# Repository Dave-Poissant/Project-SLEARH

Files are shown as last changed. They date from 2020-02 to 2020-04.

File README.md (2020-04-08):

# Project-SLEARH
Articulated robotic hand designed for sign language education

# Preriquisites:
Hardware:
  - Arduino Mega 2560;
  - 1 usb to printer type cable;
  - 1 drive for the motors ( (PCA-96 85) link: https://www.sunfounder.com/pca9685-16-channel-12-bit-pwm-servo-driver.html);
  - 12 electrical step motors ((TowerPro SG90 Mini-engrenage Micro Servo 9g) link: https://lamassue.fr/product/towerpro-sg90-mini-engrenage-micro-servo-9g/);
  - RaspberryPi 3B+;
  - Micro-SD card (for RPi image);
  
Software;
  - Python 3.7(installed for this gitProject, but not necessarily needed);
  - Python Library:
    - pySerial;
    - tkinter;
  - Arduino IDE for the compiler;
  - Arduino Library:
    - Adafruit_PWMServoDriver.h;
    - ArduinoJson.h;
    - Wire.h;
    (But they all should be downloaded with the plateformio.ini)
    
# Steps to start your project:
  - Read the Mechanics/README.md for informations on how to build the hand;
  - Read the Electrics/README.md for informations on how to plug the motors and the drive on the arduino;
  - Install your favorite python IDE;
  - Open this git repo in a new project and create a python RunTool for UI_Main_Script.py script (that's where the application starts);
  - Install pySerial on your computer (it will appears in your python <python path>/Lib/*);
  (Now, your python side of the project should be up to run)
  - Install VsCode on your computer;
  - Install plateformio and ArduinoIDE in your vscode;
  - Set your Arduino_debug.exe path in your VsCode setups;
  - Build the project one first time (and it should load all the needed libraries);
  (Now, your Arduino side of the project should be up to run)

  - Plug the Arduino to your computer and start the UI_Main_Script.py to start the application and the Arduino thread!
  
 # Steps to be able to run to application on the Raspberry Pi 3b+
  - Flash your Micro-SD card with an up to date RPi image running a linux operating system (you can flash your Micro-SD card with this       tool: https://www.balena.io/etcher/);
  - Connect your Micro-SD card in your RPi and open it with an internet cable or via VMWare for example;
  - On the first RPi's run, set your preferences;
  - Now, open a terminal and instal python 3.6 (or niewer, this could take some time) (this link could be usefull: https://github.com/instabot-py/instabot.py/wiki/Installing-Python-3.7-on-Raspberry-Pi);
  - Install the PySerial library with:
    $ sudo apt-get install pyserial
  - If you're connected to your RPi via VMWare or ssh, run this command:
    - $ export DISPLAY=:0
  - Create your project directory where you want it on your RPi:
    - $ cd "DIRECTORY PATH"
    - $ mkdir "PROJECT NAME"
    - $ cd "PROJECT NAME"
    - $ git clone "THE PROJECT'S LINK"
    - $ git pull
  - The project should now be copied locally onto your RPi;
  
  - Now go to the project's Ui_Main_script.py path on your RPi and run the program through a terminal:
    - $ python Ui_Main_Script.py
  
# Now Have Fun !

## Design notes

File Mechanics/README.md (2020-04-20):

ASSEMBLY OF THE HAND

1. Start by opening the BOM file in this folder.
2. With a 3D printer at 40% fill and supports, print all the parts that have &quot;3D printed&quot; as a link. Some parts need to be printed more than once, refer to the quantity column of the BOM to know how many.
3. Make sure you have at your disposition all the fasteners needed for the assembly. The specs and the quantity needed are given in the BOM. If you need to buy anything, there is a McMaster link for each part.
4. Separate all the printed parts for each of the fingers where each number is the index in the BOM;

Pinky: 4 – 1 – 12 – 7

Ring finger: 4 – 1 – 12 – 3

Middle finger: 4 – 1 – 12 – 5

Index finger: 4 – 1 – 12 – 3

Thumb: 8 – 9 – 10 – 11 – 27 - 28

1. For the pinky, attach the two phalanxes together at the joint with the bolt of index 17 and the nut of index 19.
2. Assemble a servomotor to the servosocket with the fasteners 24. Make sure the wires are towards the hand.
3. Install the second lever arm on the servomotor with the bolt of index 15 and the nut of index 16. Make sure the curve of the rod is toward the back of the finger, that the head of the bolt is toward the servomotor and that you use the small hole of the rod.
4. Attach the other end of the rod to the last phalanx with the bolt of index 18 and the nut of index 19.
5. Attach the first lever arm of index 1 on the small arm of the first phalanx with the bolt of index 18 and the nut of index 19. Make sure the rod is towards the outside of the phalanx, that you use the bigger hole of the rod and that the curve is towards the back of the finger.
6. Repeat the steps 5-9 for each of the other fingers except for the thumb.
7. For the thumb, attach the two last phalanxes together at the joint with the bolt of index 17 and the nut of index 19.
8. Assemble a servomotor to the two servosockets of the thumb with the fasteners 24. Make sure the wires are towards the hand.
9. Install the third lever arm on the servomotor of the second servosocket with the bolt of index 15 and the nut of index 16. Make sure the curve of the rod is toward the back of the finger, that the head of the bolt is toward the servomotor and that you use the small hole of the rod.
10. Attach the other end of the rod to the last phalanx with the bolt of index 18 and the nut of index 19.
11. Install the second lever arm on the servomotor of the first servosocket with the bolt of index 15 and the nut of index 16. Make sure the curve of the rod is toward the back of the finger, that the head of the bolt is toward the servomotor and that you use the small hole of the rod.
12. Attach the other end of the rod to the second phalanx with the bolt of index 18 and the nut of index 19.
13. Attach the first lever arm on the small arm of the first phalanx with the bolt of index 25 and the nut of index 26. Make sure the rod is towards the back of the phalanx, that you use the bigger hole of the rod and that the curve is towards the outside of the finger.
14. Install a servomotor in each of the 4 servo holders for the palm (index 6). Use the fasteners 24 and make sure that it is installed so that viewed from the top of the servomotor, the wires go to the right.
15. Install the four assemblies made at step 19 on the palm with the fasteners of index 24. Make sure the arms of the servomotors are towards the thumb and that the wires are towards the base of the hand.
16. Install a servomotor on the palm at its spot near the thumb joint. Make sure the wires go towards the hand.
17. Install all the fingers except of the thumb on the palm, use the bolt of index 17 and the nut of index 19.
18. Install the thumb on the palm with the bolt of index 25 and the nut of index 26.
19. Install the lever arms of the fingers on the servomotors of the palm with the bolt of index 15 and the nut of index 16.
20. Install the motors drive on the back of the hand with the four bolts of index 23.
21. Make all the electric connections as explained in the electric README.
22. With three bolts of index 15, install a «+» shape servomotor arm on the base of the palm.
23. With the bolts of index 20, install the Arduino and the raspberry pi on the base of the arm.
24. Install the arm on the base with four bolts of index 20.
25. Install the last servo at the top of the arm with fasteners of index 24.
26. Pass all the wires of the hand inside the arm and make the connections as explained in the electric README.
27. Install the hand on the servomotor.

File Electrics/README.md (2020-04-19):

# Electrical Parts list

    Name	              Description	                                Quantity
    ------------------------------------------------------------------------
    Arduino board	      Arduino Mega 2560	                              1
    Servo driver	      PCA9685 16 channel PWM servo Driver	          1
    Servo motors	      SG90 servo motor	                              12

# Electrical Connections:

  # Arduino pins:
    - 5V:         Ard1 -------> Dr6
    - Gnd:        Ard2 -------> Dr3
    - Vin:        Ard3 -------> Dr7
    - Gnd:        Ard4 -------> Dr1
    - 5V:         Ard5 -------> Dr2
    - scl(pin21): Ard6 -------> Dr4
    - sda(pin20): Ard7 -------> Dr5
    
  # Drive pins:
    - Gnd:        Dr1 --------> Ard4
    - V+:         Dr2 --------> Ard5
    - Gnd:        Dr3 --------> Ard2
    - scl         Dr4 --------> Ard6
    - sda         Dr5 --------> Ard7
    - Vcc         Dr6 --------> Ard1
    - V+          Dr7 --------> Ard3
    
    - 0           Dr8 --------> motor 0
    - 1           Dr9 --------> motor 1
    - 2           Dr10 -------> motor 2
    - 3           Dr11 -------> motor 3
    - 4           Dr12 -------> motor 4
    - 5           Dr13 -------> motor 5
    - 6           Dr14 -------> motor 6
    - 7           Dr15 -------> motor 7
    - 8           Dr16 -------> motor 8
    - 9           Dr17 -------> motor 9

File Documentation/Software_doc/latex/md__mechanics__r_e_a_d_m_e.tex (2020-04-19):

A\+S\+S\+E\+M\+B\+LY OF T\+HE H\+A\+ND

\begin{DoxyEnumerate}
\item Start by 3D printing all the parts of this folder.
\item Separate the pieces for each of the fingers.
\item Put the Servomotors in each of the 10 sockets with the screws with the cables going to the hand.
\item For each finger, assemble the two phalanxes together with a 1/8\textquotesingle{}\textquotesingle{} bolt and a nut.
\item For the servomotors in the fingers, attach the small hole of the small rod with a 1/16\textquotesingle{}\textquotesingle{} bolt and a nut.
\item Attach the other end of the small rod to the upside attach of the distant phalanx.
\item Attach the finger to the palm with a 1/8\textquotesingle{}\textquotesingle{} bolt and a nut.
\item Attach the big hole of the big rod on the attach of the first phalanx of each finger with a 1/8\textquotesingle{}\textquotesingle{} rod and a nut.
\item Attach the last hole of the big rod on the servomotor with a 1/16\textquotesingle{}\textquotesingle{} bolt and a nut. 
\end{DoxyEnumerate}

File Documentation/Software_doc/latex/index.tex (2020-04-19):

\hypertarget{index_Python}{}\doxysection{Python}\label{index_Python}
The Python code englobe the UI and the back-\/end of if\hypertarget{index_Arduino}{}\doxysection{Arduino}\label{index_Arduino}
The Arduino code englobe the function related to motors control sign execution

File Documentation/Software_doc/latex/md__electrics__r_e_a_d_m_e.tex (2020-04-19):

\hypertarget{md__electrics__r_e_a_d_m_e_autotoc_md1}{}\doxysection{Arduino pins\+:}\label{md__electrics__r_e_a_d_m_e_autotoc_md1}

\begin{DoxyItemize}
\item 5V\+: Ard1 -\/-\/-\/-\/---$>$ Dr6
\item Gnd\+: Ard2 -\/-\/-\/-\/---$>$ Dr3
\item Vin\+: Ard3 -\/-\/-\/-\/---$>$ Dr7
\item Gnd\+: Ard4 -\/-\/-\/-\/---$>$ Dr1
\item 5V\+: Ard5 -\/-\/-\/-\/---$>$ Dr2
\item scl(pin21)\+: Ard6 -\/-\/-\/-\/---$>$ Dr4
\item sda(pin20)\+: Ard7 -\/-\/-\/-\/---$>$ Dr5
\end{DoxyItemize}\hypertarget{md__electrics__r_e_a_d_m_e_autotoc_md2}{}\doxysection{Drive pins\+:}\label{md__electrics__r_e_a_d_m_e_autotoc_md2}

\begin{DoxyItemize}
\item Gnd\+: Dr1 -\/-\/-\/-\/-\/---$>$ Ard4
\item V+\+: Dr2 -\/-\/-\/-\/-\/---$>$ Ard5
\item Gnd\+: Dr3 -\/-\/-\/-\/-\/---$>$ Ard2
\item scl Dr4 -\/-\/-\/-\/-\/---$>$ Ard6
\item sda Dr5 -\/-\/-\/-\/-\/---$>$ Ard7
\item Vcc Dr6 -\/-\/-\/-\/-\/---$>$ Ard1
\item V+ Dr7 -\/-\/-\/-\/-\/---$>$ Ard3
\item 0 Dr8 -\/-\/-\/-\/-\/---$>$ motor 0
\item 1 Dr9 -\/-\/-\/-\/-\/---$>$ motor 1
\item 2 Dr10 -\/-\/-\/-\/---$>$ motor 2
\item 3 Dr11 -\/-\/-\/-\/---$>$ motor 3
\item 4 Dr12 -\/-\/-\/-\/---$>$ motor 4
\item 5 Dr13 -\/-\/-\/-\/---$>$ motor 5
\item 6 Dr14 -\/-\/-\/-\/---$>$ motor 6
\item 7 Dr15 -\/-\/-\/-\/---$>$ motor 7
\item 8 Dr16 -\/-\/-\/-\/---$>$ motor 8
\item 9 Dr17 -\/-\/-\/-\/---$>$ motor 9 
\end{DoxyItemize}

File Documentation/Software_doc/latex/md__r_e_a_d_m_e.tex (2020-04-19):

Articulated robotic hand designed for sign language education\hypertarget{md__r_e_a_d_m_e_autotoc_md4}{}\doxysection{Preriquisites\+:}\label{md__r_e_a_d_m_e_autotoc_md4}
Hardware\+:
\begin{DoxyItemize}
\item Arduino Mega 2560;
\item 1 usb to printer type cable;
\item 1 drive for the motors ( (P\+C\+A-\/96 85) link\+: \href{https://www.sunfounder.com/pca9685-16-channel-12-bit-pwm-servo-driver.html}{\texttt{ https\+://www.\+sunfounder.\+com/pca9685-\/16-\/channel-\/12-\/bit-\/pwm-\/servo-\/driver.\+html}});
\item 12 electrical step motors ((Tower\+Pro S\+G90 Mini-\/engrenage Micro \mbox{\hyperlink{class_servo}{Servo}} 9g) link\+: \href{https://lamassue.fr/product/towerpro-sg90-mini-engrenage-micro-servo-9g/}{\texttt{ https\+://lamassue.\+fr/product/towerpro-\/sg90-\/mini-\/engrenage-\/micro-\/servo-\/9g/}});
\item Raspberry\+Pi 3B+;
\item Micro-\/\+SD card (for R\+Pi image);
\end{DoxyItemize}

Software;
\begin{DoxyItemize}
\item Python 3.\+7(installed for this git\+Project, but not necessarily needed);
\item Python Library\+:
\begin{DoxyItemize}
\item py\+Serial;
\item tkinter;
\end{DoxyItemize}
\item Arduino I\+DE for the compiler;
\item Arduino Library\+:
\begin{DoxyItemize}
\item Adafruit\+\_\+\+P\+W\+M\+Servo\+Driver.\+h;
\item Arduino\+Json.\+h;
\item Wire.\+h; (But they all should be downloaded with the plateformio.\+ini)
\end{DoxyItemize}
\end{DoxyItemize}\hypertarget{md__r_e_a_d_m_e_autotoc_md5}{}\doxysection{Steps to start your project\+:}\label{md__r_e_a_d_m_e_autotoc_md5}

\begin{DoxyItemize}
\item Read the Mechanics/\+R\+E\+A\+D\+M\+E.\+md for informations on how to build the hand;
\item Read the Electrics/\+R\+E\+A\+D\+M\+E.\+md for informations on how to plug the motors and the drive on the arduino;
\item Install your favorite python I\+DE;
\item Open this git repo in a new project and create a python Run\+Tool for U\+I\+\_\+\+Main\+\_\+\+Script.\+py script (that\textquotesingle{}s where the application starts);
\item Install py\+Serial on your computer (it will appears in your python $<$python path$>$/\+Lib/$\ast$); (Now, your python side of the project should be up to run)
\item Install Vs\+Code on your computer;
\item Install plateformio and Arduino\+I\+DE in your vscode;
\item Set your Arduino\+\_\+debug.\+exe path in your Vs\+Code setups;
\item Build the project one first time (and it should load all the needed libraries); (Now, your Arduino side of the project should be up to run)
\item Plug the Arduino to your computer and start the U\+I\+\_\+\+Main\+\_\+\+Script.\+py to start the application and the Arduino thread!
\end{DoxyItemize}\hypertarget{md__r_e_a_d_m_e_autotoc_md6}{}\doxysection{Steps to be able to run to application on the Raspberry Pi 3b+}\label{md__r_e_a_d_m_e_autotoc_md6}

\begin{DoxyItemize}
\item Flash your Micro-\/\+SD card with an up to date R\+Pi image running a linux operating system (you can flash your Micro-\/\+SD card with this tool\+: \href{https://www.balena.io/etcher/}{\texttt{ https\+://www.\+balena.\+io/etcher/}});
\item Connect your Micro-\/\+SD card in your R\+Pi and open it with an internet cable or via V\+M\+Ware for example;
\item On the first R\+Pi\textquotesingle{}s run, set your preferences;
\item Now, open a terminal and instal python 3.\+6 (or niewer, this could take some time) (this link could be usefull\+: \href{https://github.com/instabot-py/instabot.py/wiki/Installing-Python-3.7-on-Raspberry-Pi}{\texttt{ https\+://github.\+com/instabot-\/py/instabot.\+py/wiki/\+Installing-\/\+Python-\/3.\+7-\/on-\/\+Raspberry-\/\+Pi}});
\item Install the Py\+Serial library with\+: \$ sudo apt-\/get install pyserial
\item If you\textquotesingle{}re connected to your R\+Pi via V\+M\+Ware or ssh, run this command\+:
\begin{DoxyItemize}
\item \$ export D\+I\+S\+P\+L\+AY=\+:0
\end{DoxyItemize}
\item Create your project directory where you want it on your R\+Pi\+:
\begin{DoxyItemize}
\item \$ cd \char`\"{}\+D\+I\+R\+E\+C\+T\+O\+R\+Y P\+A\+T\+H\char`\"{}
\item \$ mkdir \char`\"{}\+P\+R\+O\+J\+E\+C\+T N\+A\+M\+E\char`\"{}
\item \$ cd \char`\"{}\+P\+R\+O\+J\+E\+C\+T N\+A\+M\+E\char`\"{}
\item \$ git clone \char`\"{}\+T\+H\+E P\+R\+O\+J\+E\+C\+T\textquotesingle{}\+S L\+I\+N\+K\char`\"{}
\item \$ git pull
\end{DoxyItemize}
\item The project should now be copied locally onto your R\+Pi;
\item Now go to the project\textquotesingle{}s Ui\+\_\+\+Main\+\_\+script.\+py path on your R\+Pi and run the program through a terminal\+:
\begin{DoxyItemize}
\item \$ python Ui\+\_\+\+Main\+\_\+\+Script.\+py
\end{DoxyItemize}
\end{DoxyItemize}\hypertarget{md__r_e_a_d_m_e_autotoc_md7}{}\doxysection{Now Have Fun !}\label{md__r_e_a_d_m_e_autotoc_md7}

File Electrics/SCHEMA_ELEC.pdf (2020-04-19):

SDA
SCL

5V

GND

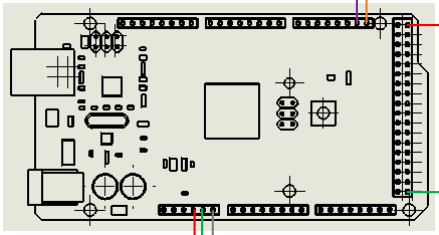
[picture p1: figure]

Vin
5V
GND

ARDUINO MEGA 2560

SERVO SG90

1
SERVO SG90

2
SERVO SG90

3
SERVO SG90

4
SERVO SG90

5
SERVO SG90

6
SERVO SG90

7
SERVO SG90

8
SERVO SG90

9
SERVO SG90

-10
SERVO SG90

-11
SERVO SG90

-12

PCA9685
16 CHANNEL 12

-BIT PWM
I2C ADDRESS l[A5..A0][R/W] VDD : 2.3

-5.5V IO : 5V SAFE
OUTPUT : 25mA EACH/400mA TOTAL GND
SDA
SCL
#OE

VCC
V+

EXTCLK
A0
A1
A2
A3
A4
A5

GND

PWM0
PWM1
PWM2
PWM3
PWM4
PWM5
PWM6
PWM7
PWM8
PWM9
PWM10
PWM11
PWM12
PWM13
PWM14
PWM15
AUXILIARY POWER
V+
GND
GND EXTCLK WHEN NOT IN USE

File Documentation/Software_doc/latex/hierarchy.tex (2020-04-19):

\doxysection{Class Hierarchy}
This inheritance list is sorted roughly, but not completely, alphabetically\+:\begin{DoxyCompactList}
\item \contentsline{section}{character}{\pageref{structcharacter}}{}
\item \contentsline{section}{Python\+\_\+project.\+Backend\+\_\+\+Scripts.\+Communication.\+Communication}{\pageref{class_python__project_1_1_backend___scripts_1_1_communication_1_1_communication}}{}
\item \contentsline{section}{Communication\+Arduino}{\pageref{class_communication_arduino}}{}
\item \contentsline{section}{Python\+\_\+project.\+Backend\+\_\+\+Scripts.\+Configuration.\+Configuration}{\pageref{class_python__project_1_1_backend___scripts_1_1_configuration_1_1_configuration}}{}
\item \contentsline{section}{Python\+\_\+project.\+Backend\+\_\+\+Scripts.\+Event.\+Event}{\pageref{class_python__project_1_1_backend___scripts_1_1_event_1_1_event}}{}
\item \contentsline{section}{Python\+\_\+project.\+Backend\+\_\+\+Scripts.\+Event\+Handler.\+Event\+Handler}{\pageref{class_python__project_1_1_backend___scripts_1_1_event_handler_1_1_event_handler}}{}
\item \contentsline{section}{Python\+\_\+project.\+Backend\+\_\+\+Scripts.\+Event\+Queue.\+Event\+Queue}{\pageref{class_python__project_1_1_backend___scripts_1_1_event_queue_1_1_event_queue}}{}
\item Frame\begin{DoxyCompactList}
\item \contentsline{section}{Python\+\_\+project.\+Ui\+\_\+\+Main\+\_\+\+Script.\+application}{\pageref{class_python__project_1_1_ui___main___script_1_1application}}{}
\end{DoxyCompactList}
\item \contentsline{section}{Python\+\_\+project.\+Backend\+\_\+\+Scripts.\+Quiz.\+Quiz}{\pageref{class_python__project_1_1_backend___scripts_1_1_quiz_1_1_quiz}}{}
\item \contentsline{section}{Servo}{\pageref{class_servo}}{}
\item \contentsline{section}{Soft\+Timer}{\pageref{class_soft_timer}}{}
\item \contentsline{section}{Python\+\_\+project.\+Backend\+\_\+\+Scripts.\+Text\+Analyser.\+Text\+Analyser}{\pageref{class_python__project_1_1_backend___scripts_1_1_text_analyser_1_1_text_analyser}}{}
\item Enum\begin{DoxyCompactList}
\item \contentsline{section}{Python\+\_\+project.\+Backend\+\_\+\+Scripts.\+Event\+Type.\+Event\+Type}{\pageref{class_python__project_1_1_backend___scripts_1_1_event_type_1_1_event_type}}{}
\item \contentsline{section}{Python\+\_\+project.\+Backend\+\_\+\+Scripts.\+Logger.\+Color}{\pageref{class_python__project_1_1_backend___scripts_1_1_logger_1_1_color}}{}
\item \contentsline{section}{Python\+\_\+project.\+Backend\+\_\+\+Scripts.\+Purpose.\+Purpose}{\pageref{class_python__project_1_1_backend___scripts_1_1_purpose_1_1_purpose}}{}
\item \contentsline{section}{Python\+\_\+project.\+Ui\+\_\+\+Main\+\_\+\+Script.\+Mode\+Enum}{\pageref{class_python__project_1_1_ui___main___script_1_1_mode_enum}}{}
\item \contentsline{section}{Python\+\_\+project.\+Ui\+\_\+\+Main\+\_\+\+Script.\+Purpose\+Enum}{\pageref{class_python__project_1_1_ui___main___script_1_1_purpose_enum}}{}
\end{DoxyCompactList}
\end{DoxyCompactList}

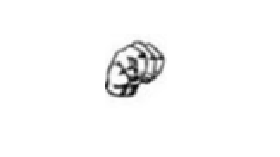
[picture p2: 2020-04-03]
Python_project/Image_Library/Quiz_purpose_img/sign_m.png

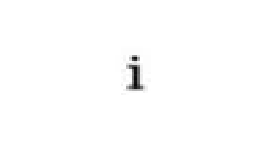
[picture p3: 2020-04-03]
Python_project/Image_Library/Education_purpose_img/letter_i.png

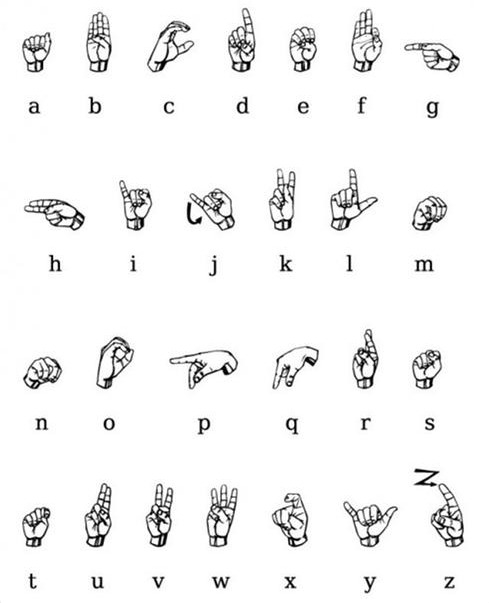
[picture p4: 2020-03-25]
Python_project/Image_Library/all_signs_img.png

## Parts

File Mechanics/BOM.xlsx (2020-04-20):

BOM
index | name | link | qty. | description | directory
1 | joint doigt palm servosocket | 3D printed | 4 | First lever arms for fingers | Project-SLEARH/Mechanics/CAD/CAD Palm/Joint_doigt_Palm-ServoSocket.SLDPRT (https://github.com/Dave-Poissant/Project-SLEARH)
2 | palm v3 | 3D printed | 1 | palm | Project-SLEARH/Mechanics/CAD/CAD Palm/PalmV3.SLDPRT
3 | phalange 2 index-anulaire | 3D printed | 2 | Last part for index and ring finger | Project-SLEARH/Mechanics/CAD/CAD Palm/CAD Index-Annulaire/phalange2_Index-Annulaire.SLDPRT
4 | SG90 Servo socket | 3D printed | 4 | Socket for servo for each finger | Project-SLEARH/Mechanics/CAD/CAD Palm/CAD Majeur/SG90 - Servo Socket.SLDPRT
5 | phalange 2 majeur | 3D printed | 1 | Last part for the middle finger | Project-SLEARH/Mechanics/CAD/CAD Palm/CAD Majeur/phalange2_Majeur.SLDPRT
6 | servoholder | 3D printed | 4 | Servo holders on the palm | Project-SLEARH/Mechanics/CAD/CAD Palm/ServoHolder.SLDPRT
7 | phalange 2 auriculaire | 3D printed | 1 | Last part for the pinky finger | Project-SLEARH/Mechanics/CAD/CAD Palm/CAD Auriculaire/phalange2_Auriculaire.SLDPRT
8 | phalange 2 pouce | 3D printed | 1 | Last part for the thumb | Project-SLEARH/Mechanics/CAD/CAD Palm/CAD Pouce/Pouce/phalange2_Pouce.SLDPRT
9 | Bras de levier pouce | 3D printed | 1 | Last lever arm for the thumb | Project-SLEARH/Mechanics/CAD/CAD Palm/CAD Pouce/Pouce/Bras de levier_Pouce.SLDPRT
10 | Bras de levier pouce 2 | 3D printed | 1 | Second lever arm for the thumb | Project-SLEARH/Mechanics/CAD/CAD Palm/CAD Pouce/Bras de levier_Pouce2.SLDPRT
11 | Bras de levier pouce 3 | 3D printed | 1 | First lever arm for the thumb | Project-SLEARH/Mechanics/CAD/CAD Palm/CAD Pouce/Bras de levier_Pouce3.SLDPRT
12 | Bras de levier | 3D printed | 4 | Second lever arms for fingers | Project-SLEARH/Mechanics/CAD/CAD Palm/CAD Majeur/Bras de levier.SLDPRT
13 | Bras | 3D printed | 1 | Arm | Project-SLEARH/Mechanics/CAD/CAD Socle/Bras.SLDPRT
14 | Base | 3D printed | 1 | Base for the arm | Project-SLEARH/Mechanics/CAD/CAD Socle/Base.SLDPRT
15 | 92453A856 | https://www.mcmaster.com/92453a856 | 15 | 00-90 Thread, 3/8" Long -- lever arm to servo | Project-SLEARH/Mechanics/CAD/CAD Palm/92453A856_BRASS ROUND HEAD SLOTTED MACHINE SCREW.SLDPRT
16 | 90001A403 | https://www.mcmaster.com/90001a403 | 11 | 00-90 Thread Size -- lever arm to servo | Project-SLEARH/Mechanics/CAD/CAD Palm/90001A403_TYPE 18-8 STAINLESS STEEL HEX NUT.SLDPRT
17 | 92196A131 | https://www.mcmaster.com/92196a131 | 10 | 5-40 Thread Size, 3/4" Long -- point pivot of sockets to palm | Project-SLEARH/Mechanics/CAD/CAD Palm/92196A131_18-8 STAINLESS STEEL SOCKET HEAD CAP SCREW.SLDPRT
18 | 91251A130 | https://www.mcmaster.com/91251a130 | 10 | 5-40 Thread Size, 5/8" Long -- lever arms to sockets and tips of fingers | Project-SLEARH/Mechanics/CAD/CAD Palm/91251A130_BLACK-OXIDE ALLOY STEEL SOCKET HEAD CAP SCREW.SLDPRT
19 | 90480A006 | https://www.mcmaster.com/90480a006 | 20 | Zinc-Plated, 5-40 Thread Size -- knot for 14 and 15 | Project-SLEARH/Mechanics/CAD/CAD Palm/90480A006_LOW-STRENGTH STEEL HEX NUT.SLDPRT
20 | 92000A106 | https://www.mcmaster.com/92000a106 | 14 | M2.5 x 0.45mm Thread, 10mm Long -- Arduino Mega, Raspberry Pi and arm | Project-SLEARH/Mechanics/CAD/CAD Socle/92000A106_18-8 SS METRIC PAN HEAD PHIL MACHINE SCREW.SLDPRT
21 | 90480A003 | https://www.mcmaster.com/90480a003 | 1 | Zinc-Plated, 2-56 Thread Size -- first lever arm to socket of the thumb | Project-SLEARH/Mechanics/CAD/CAD Palm/90480A003_LOW-STRENGTH STEEL HEX NUT.SLDPRT
22 | 91251A079 | https://www.mcmaster.com/91251a079 | 1 | 2-56 Thread Size, 3/8" Long -- first lever arm to socket of the thumb | Project-SLEARH/Mechanics/CAD/CAD Palm/91251A079_BLACK-OXIDE ALLOY STEEL SOCKET HEAD CAP SCREW.SLDPRT
23 | 90087A103 | https://www.mcmaster.com/90087a103 | 4 | Zinc-Plated Steel, 2-56 Thread, 3/8" Long -- for drive | Project-SLEARH/Mechanics/CAD/CAD Palm/90087A103_THRD-CUTTING SCREW FOR METAL PLASTIC TYPE F.SLDPRT
24 | 99461A825 | https://www.mcmaster.com/99461a825 | 30 | for Plastic, 18-8 Stainless Steel, Number 3 Size, 3/8" Long -- for servo and servo holders | Project-SLEARH/Mechanics/CAD/CAD Palm/99461A825_THREAD-FORMING SCREW FOR PLASTIC.SLDPRT
25 | 90044A242 | https://www.mcmaster.com/90044a242 | 1 | 2-64 Thread Size, 1" Long -- first joint of thumb | Project-SLEARH/Mechanics/CAD/CAD Palm/90044A242_BLACK-OXIDE ALLOY STEEL SOCKET HEAD SCREW.SLDPRT
26 | 90480A135 | https://www.mcmaster.com/90480a135 | 1 | Zinc-Plated, 2-64 Thread Size -- first joint of thumb | Project-SLEARH/Mechanics/CAD/CAD Palm/90480A135_LOW-STRENGTH STEEL HEX NUT.SLDPRT
27 | SG90 Servo socket pouce | 3D printed | 1 | Second socket for servo for the thumb | Project-SLEARH/Mechanics/CAD/CAD Palm/CAD Pouce/Pouce/SG90 - Servo Socket_Pouce.SLDPRT
28 | SG90 Servo socket pouce 2 | 3D printed | 1 | First socket for servo for the thumb | Project-SLEARH/Mechanics/CAD/CAD Palm/CAD Pouce/SG90 - Servo Socket_Pouce2.SLDPRT

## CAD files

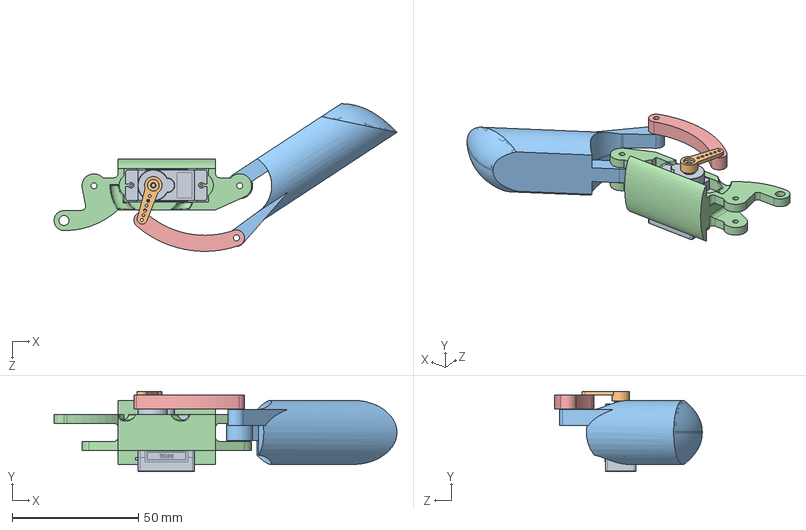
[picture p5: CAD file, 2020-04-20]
Mechanics/CAD/CAD Palm/CAD Index-Annulaire/Index-Annulaire.SLDASM
135.7 x 31.8 x 58.4 mm
SG90 - Micro Servo 9g - Tower Pro.1
SG90 - Micro Servo 9g - Tower Pro.2
phalange2_Index-Annulaire
SG90 - Servo Socket
Bras de levier

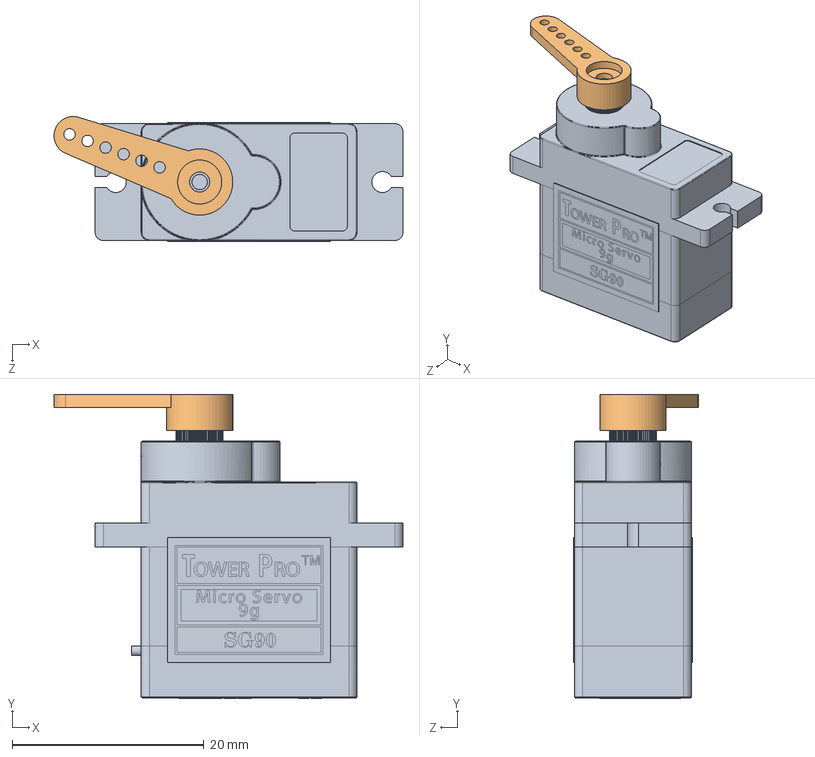
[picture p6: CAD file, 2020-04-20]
Mechanics/CAD/CAD Palm/CAD Majeur/Servo - SG90/SG90 - Micro Servo Assembly.SLDASM
36.4 x 31.8 x 13.0 mm
SG90 - Micro Servo 9g - Tower Pro.1
SG90 - Micro Servo 9g - Tower Pro.2

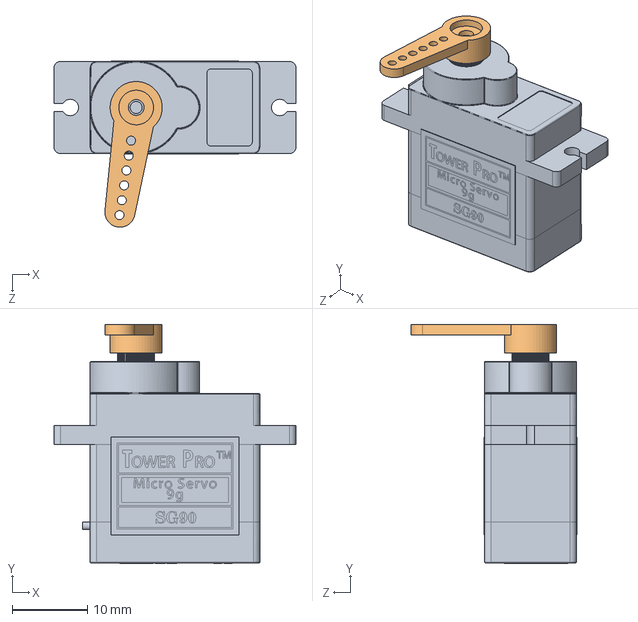
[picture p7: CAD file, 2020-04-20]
Mechanics/CAD/Servo - SG90/SG90 - Micro Servo Assembly.SLDASM
32.1 x 31.8 x 22.1 mm
SG90 - Micro Servo 9g - Tower Pro.1
SG90 - Micro Servo 9g - Tower Pro.2

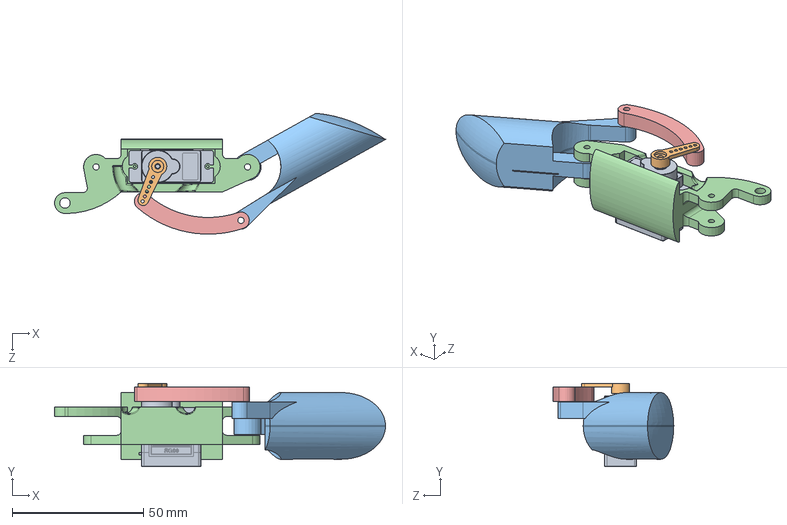
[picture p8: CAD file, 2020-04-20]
Mechanics/CAD/CAD Palm/CAD Auriculaire/Auriculaire.SLDASM
126.0 x 31.7 x 46.1 mm
SG90 - Micro Servo 9g - Tower Pro.1
SG90 - Micro Servo 9g - Tower Pro.2
phalange2_Auriculaire
SG90 - Servo Socket
Bras de levier

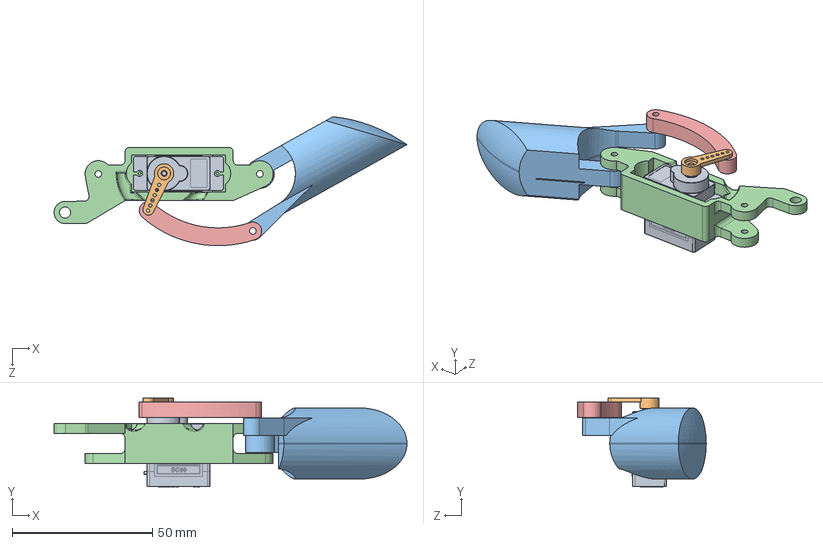
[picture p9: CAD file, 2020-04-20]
Mechanics/CAD/CAD Palm/CAD Majeur/ProximalPhalangeAssem.SLDASM
126.0 x 31.7 x 46.1 mm
SG90 - Micro Servo 9g - Tower Pro.1
SG90 - Micro Servo 9g - Tower Pro.2
phalange2
SG90 - Servo Socket
Bras de levier

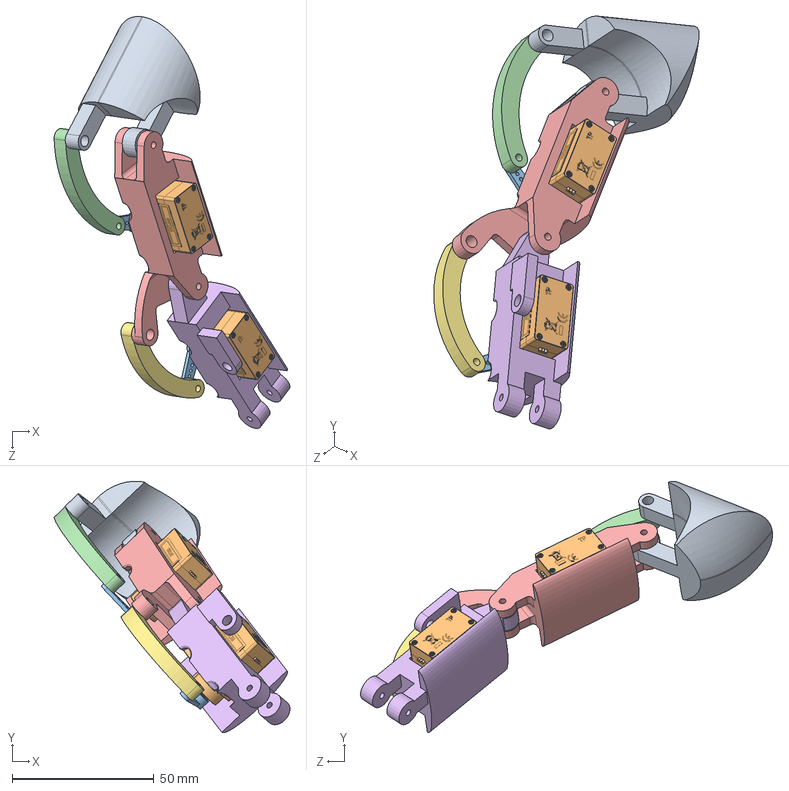
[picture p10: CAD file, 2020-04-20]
Mechanics/CAD/CAD Palm/CAD Pouce/Palm_Thumb_Ass.SLDASM
83.1 x 88.6 x 145.2 mm
phalange2_Pouce
SG90 - Micro Servo 9g - Tower Pro.1 x 2
SG90 - Micro Servo 9g - Tower Pro.2 x 2
Bras de levier_Pouce
SG90 - Servo Socket_Pouce
SG90 - Servo Socket_Pouce2
Bras de levier_Pouce2

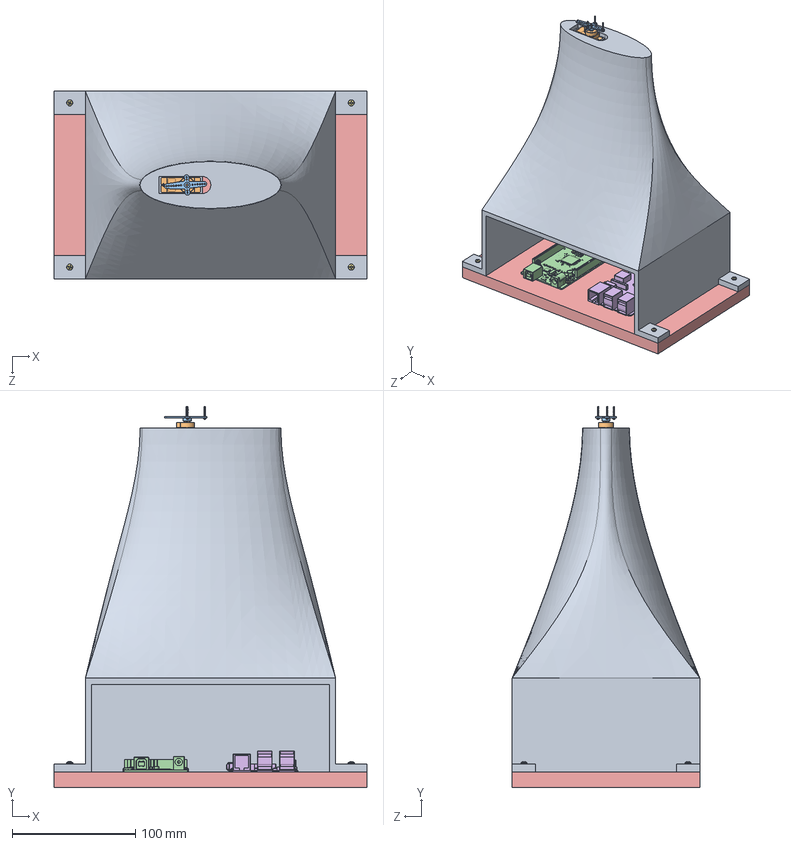
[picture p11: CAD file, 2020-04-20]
Mechanics/CAD/CAD Socle/Arm_Assembly.SLDASM
254.0 x 309.4 x 152.4 mm
Bras
SG90 - Micro Servo 9g - Tower Pro.1
SG90 - Micro Servo 9g - Tower Pro.4
arduinoMega
Base
Raspberrypimodel
92000A106_18-8 SS METRIC PAN HEAD PHIL MACHINE SCREW x 14
92453A856_BRASS ROUND HEAD SLOTTED MACHINE SCREW x 3

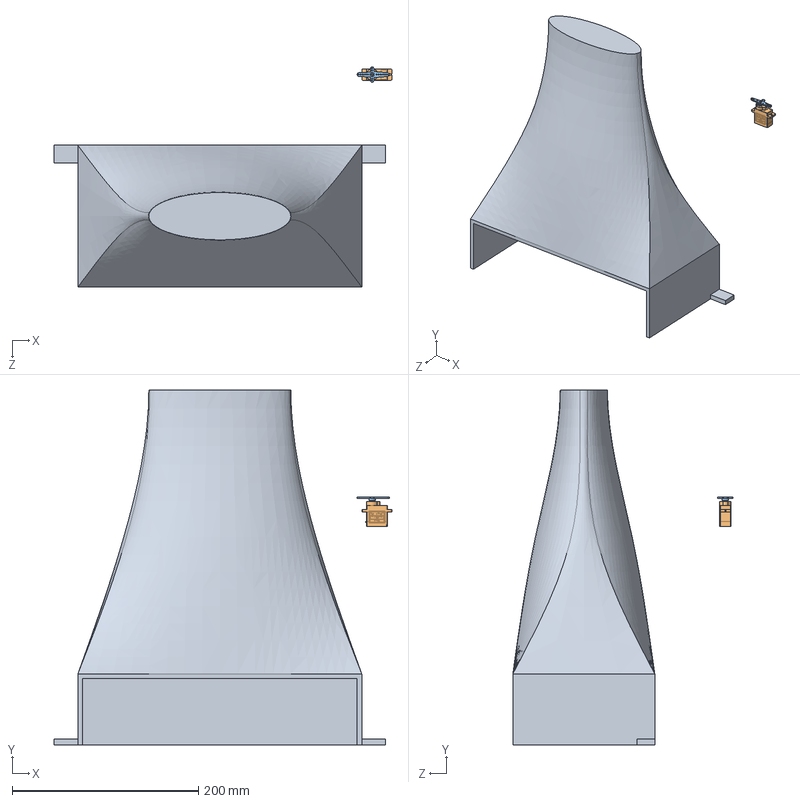
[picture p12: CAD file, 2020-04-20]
Mechanics/CAD/CAD Socle/Servo - SG90/arm_Assembly.SLDASM
362.4 x 381.0 x 236.5 mm
Bras
SG90 - Micro Servo 9g - Tower Pro.1
SG90 - Micro Servo 9g - Tower Pro.4

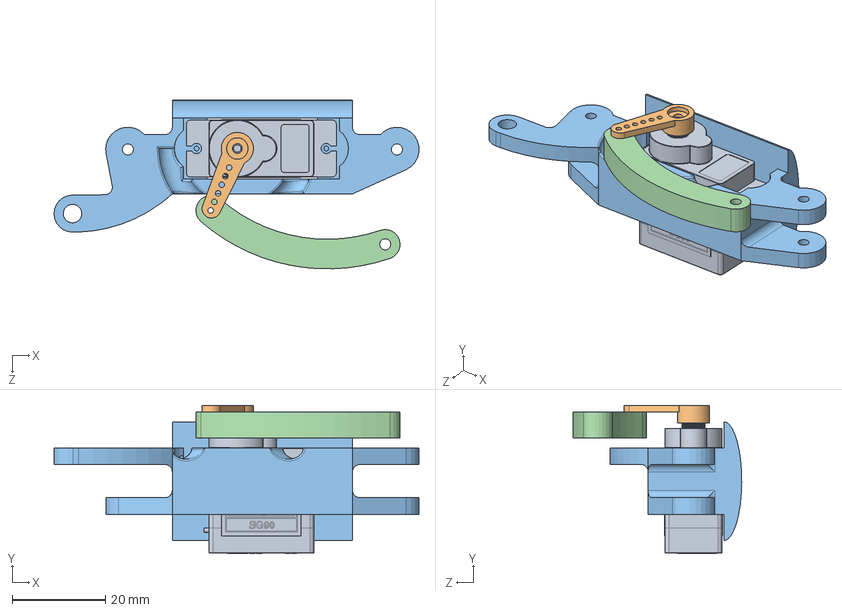
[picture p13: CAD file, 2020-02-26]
Mechanics/CAD/CAD Palm/CAD Majeur/Majeur.SLDASM
78.2 x 31.7 x 36.1 mm
SG90 - Micro Servo 9g - Tower Pro.1
SG90 - Micro Servo 9g - Tower Pro.2
SG90 - Servo Socket
Bras de levier

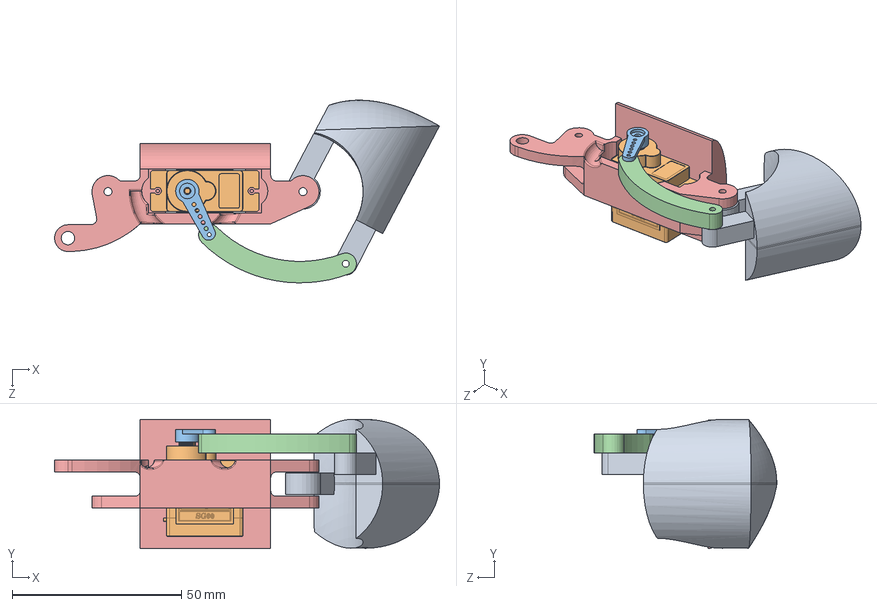
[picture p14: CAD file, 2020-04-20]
Mechanics/CAD/CAD Palm/CAD Pouce/Pouce/Pouce_Ass.SLDASM
113.9 x 38.2 x 54.0 mm
phalange2_Pouce
SG90 - Micro Servo 9g - Tower Pro.1
SG90 - Micro Servo 9g - Tower Pro.2
Bras de levier_Pouce
SG90 - Servo Socket_Pouce

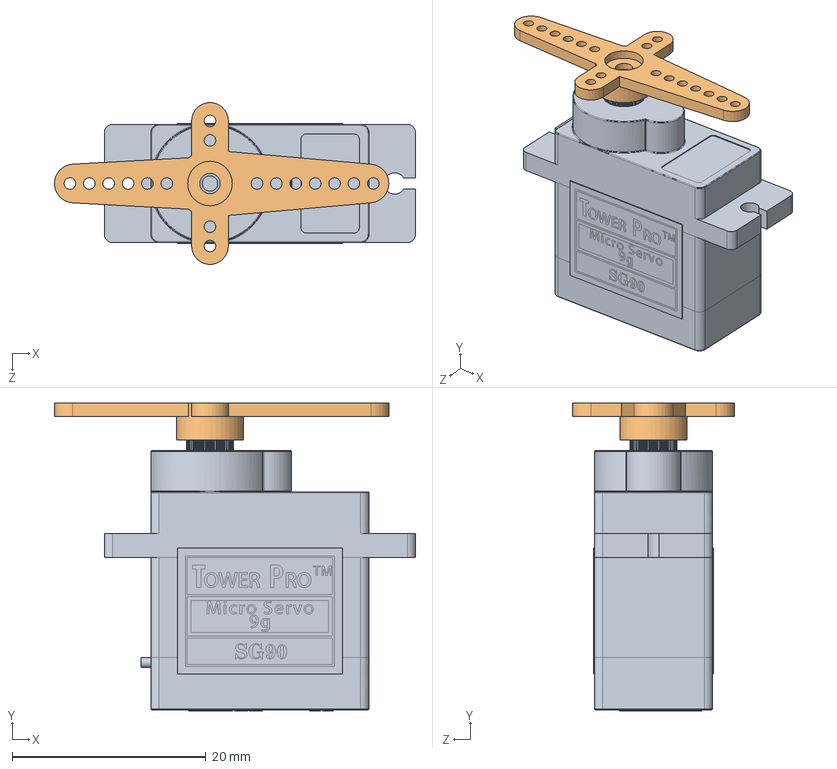
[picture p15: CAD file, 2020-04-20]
Mechanics/CAD/CAD Socle/Servo - SG90/SG90 - Micro Servo Assembly Socle.SLDASM
37.2 x 31.8 x 16.7 mm
SG90 - Micro Servo 9g - Tower Pro.1
SG90 - Micro Servo 9g - Tower Pro.4

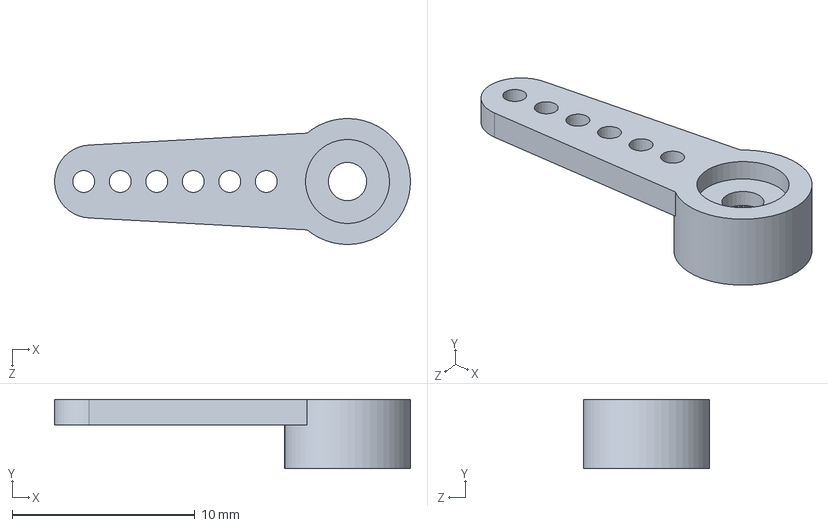
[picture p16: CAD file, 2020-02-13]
Mechanics/CAD/CAD Palm/CAD Auriculaire/Servo - SG90/SG90 - Micro Servo 9g - Tower Pro.2.SLDPRT
19.5 x 3.80 x 6.90 mm

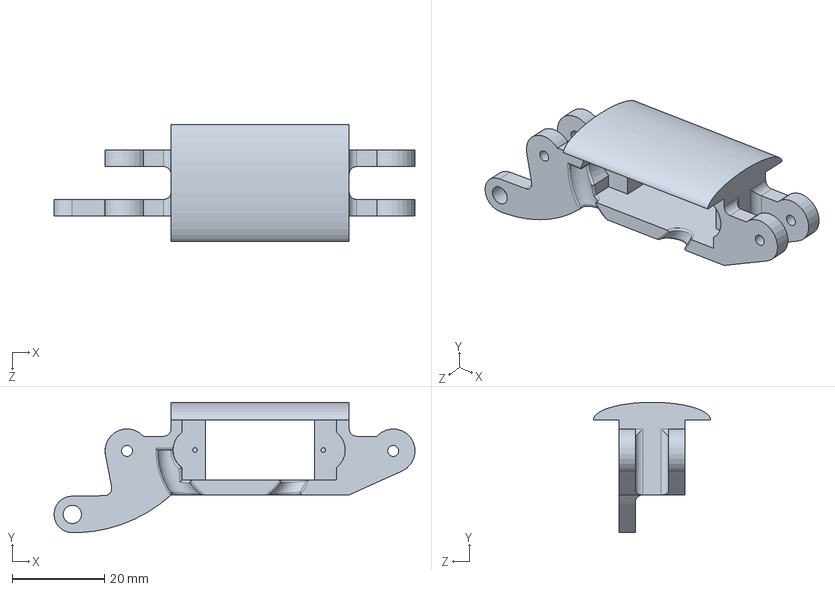
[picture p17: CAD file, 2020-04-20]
Mechanics/CAD/CAD Palm/CAD Auriculaire/SG90 - Servo Socket.SLDPRT
78.2 x 28.3 x 25.4 mm

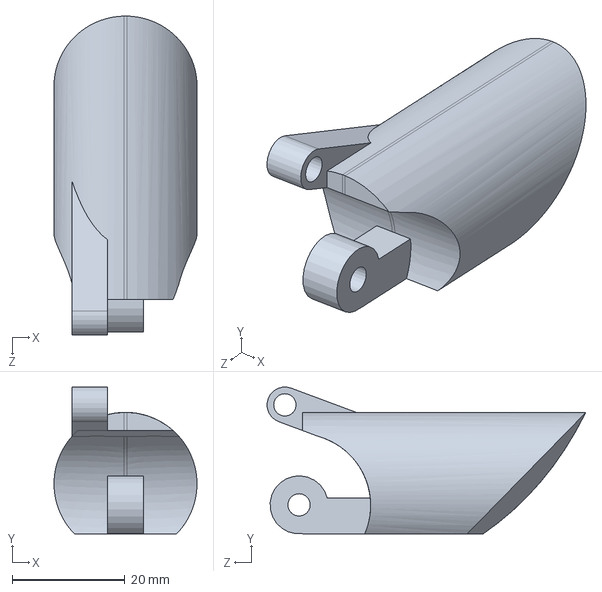
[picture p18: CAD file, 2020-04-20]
Mechanics/CAD/CAD Palm/CAD Majeur/phalange2.SLDPRT
25.4 x 26.1 x 56.6 mm

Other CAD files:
Mechanics/CAD/CAD Palm/CAD Pouce/Servo - SG90/SG90 - Micro Servo Assembly.SLDASM
Mechanics/CAD/CAD Palm/CAD Auriculaire/Servo - SG90/SG90 - Micro Servo Assembly.SLDASM
Mechanics/CAD/CAD Palm/CAD Index-Annulaire/Servo - SG90/SG90 - Micro Servo Assembly.SLDASM
Mechanics/CAD/CAD Palm/90001A403_TYPE 18-8 STAINLESS STEEL HEX NUT.SLDPRT
Mechanics/CAD/CAD Palm/90044A242_BLACK-OXIDE ALLOY STEEL SOCKET HEAD SCREW.SLDPRT
Mechanics/CAD/CAD Palm/90087A103_THRD-CUTTING SCREW FOR METAL PLASTIC TYPE F.SLDPRT
Mechanics/CAD/CAD Palm/90480A003_LOW-STRENGTH STEEL HEX NUT.SLDPRT
Mechanics/CAD/CAD Palm/90480A006_LOW-STRENGTH STEEL HEX NUT.SLDPRT
Mechanics/CAD/CAD Palm/90480A135_LOW-STRENGTH STEEL HEX NUT.SLDPRT
Mechanics/CAD/CAD Palm/91251A079_BLACK-OXIDE ALLOY STEEL SOCKET HEAD CAP SCREW.SLDPRT
Mechanics/CAD/CAD Palm/91251A130_BLACK-OXIDE ALLOY STEEL SOCKET HEAD CAP SCREW.SLDPRT
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

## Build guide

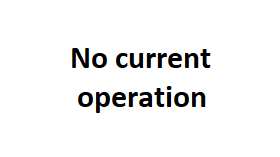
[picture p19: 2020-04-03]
Python_project/Image_Library/no_operation_img.png

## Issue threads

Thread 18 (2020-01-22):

Define user interface needs

bigemfat, 2020-01-22:

Dave-Poissant, 2020-01-22:
-> Indicator that shows the Pi-arduino connection's state;
-> Input text field, for the user;
-> A visual help for the user, to show where the process is;
-> Button to send the text to the back-end;
-> Stop button;
-> Indicator that shows if the hand is currently executing a command or if it's in idle state;
-> Manual mode and "Next letter" button;
-> A glider to select the time it takes before the next letter command is executed (If not in manual mode);
-> (Facultative) Hand simulation to show that the right commands are sent if the physical hand does not work;
-> Pause button;
-> Mode selector (Test/Quiz);
-> Warning of some sort if a letter isn't supported.

Closed 2020-01-29.

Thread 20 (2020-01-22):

Define the Back-End needs

bigemfat, 2020-01-22:

bigemfat, 2020-01-22:
**Needs for Pi :**
1. Parse and validate text input;
2. Connect to Arduino/OpenCR;
3. Update process and connection states (at all times);
4. Send messages to Arduino/OpenCR;
5. Synchronize processes;
6. Handle errors;
7. Handle options/parameters;
8. Emergency stop sequence;
9. Reset sequence;
10. Smoke test sequence (ex: move every motors);

**Need for Arduino/OpenCR :**
1.

Closed 2020-01-29.

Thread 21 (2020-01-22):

Define the back end programming classes and functions

bigemfat, 2020-01-22:

JerSamson, 2020-01-22:
**RaspberryPi classes**

1.  Parser
- Extract characters from the input text box
- Creates Event object
- Sends Events into the "Event table"

2. Event
- Has a name (character)

3. Event Handler
- Has its own thread: Executes the events in its table
- Has a private Event table
- Calls "Send comm."

4. Communication
- Communicates with the Arduino using a mutex lock condition
- Json
- Json string includes Ticket

5. Configuration
- Enum : Parameters / Options
- Has attributes for every parameter

Closed 2020-02-04.

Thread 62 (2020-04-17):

Implement reverse move functionnality and pause between letters on arduino project

bigemfat, 2020-04-17:

Closed 2020-04-19.

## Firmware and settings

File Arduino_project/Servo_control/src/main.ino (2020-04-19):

/** @file main.ino
 * @brief This file is the main program of the arduino project.
 * 
 * This file contains the main loop of the project.
 * @author CHARBONNEAU, EMILE
 * @date 19/04/2020
 */
#include <Arduino.h>
#include <string.h>
#include <Wire.h>
#include <CommunicationArduino.h>
#include "SoftTimer/SoftTimer.h"
#include "Servo.h"
/**
 * @headerfile Arduino.h "Arduino.h"
 * @headerfile string.h "string.h"
 * @headerfile Wire.h "Wire.h"
 * @headerfile CommunicationArduino.h "ArduinoCommunication.h"
 * @headerfile SoftTime/SoftTime.h "SoftTime/SoftTime.h"
 * @headerfile Servo.h "Servo.h"
 */

/** The next defined are the different communication state.
 */
#define NOT_READY_TO_SEND     false                       ///< Init. to false.
#define READY_TO_SEND         true                        ///< Init. to true.
#define NOT_READY_TO_READ     false                       ///< Init. to false.
#define READY_TO_READ         true                        ///< Init. to true.

/** The next defined are the different communication delays.
 */
#define SEND_UPDATE_PERIODE   200                         ///< sent of Read state Periode (ms)
#define READ_UPDATE_PERIODE   1000                        ///< read of Serial Periode (ms)
#define BAUD                  9600                        ///< Baud rate for Arduino mega 2560
#define LOOP_DELAY            200                         ///< time delay between each finger mouvment
#define TIME_ON_LETTER        1000                        ///< Time spent on each letter. Init. to 1 sec.

/** @brief The next defined are the different purposes.
 * The different purposes are Education and Quiz.
 * The logic of the main loop alters corresponding to the selected purpose.
 */
#define EDUCATION             0
#define QUIZ                  1
#define UNFOUND               2

/** Function prototypes
 */
void sendTimerCallback();                                 ///< callback to update the send Serial.read state
void resetTimer();                                        ///< callback to reset time spend on letter

/** Other variables
 * Communication variables:
 */
CommunicationArduino comObject = CommunicationArduino();  ///< Only instance of CommunicationArduino class, to send and read from python UI
volatile bool shouldSend = NOT_READY_TO_SEND;             ///< flag to send a message
volatile bool shouldRead = NOT_READY_TO_READ;             ///< flag to read a message
bool messageReceived = false;                             ///< flag to show if the arduino as already received a message (temporary) 
SoftTimer timerSendMsg;                                   ///< send messages timer
SoftTimer timerReadMsg;                                   ///< read messages timer (temporary)
SoftTimer timerOnLetter;                                  ///< Monitors the time spent on each letter before resetting to initial position

/** Initiating the Servo class object.
 */
Servo servo;

/** command variables
 */
bool moveDone = false;                                    ///< Flag to control the main loop according to if the hand finished moving to the desired character
bool reverseDone = false;                                 ///< Flag to control the main loop according to if the hand finished moving back to it's initial position
bool newCommand = false;                                  ///< Normaly initialized to 0. Set to 1 for testing purposes.
bool blinkState = false;                                  ///< built-in LED's blinkState
int increment = 0;                                        ///< Increment to control which finger is it's turn to be moved
int decrement = NB_FINGERS-1;                             ///< Decrement to control which finger is it's turn to be moved back to initial position
int lastCommand = toAscii(' ');                           ///< Memorizing the last command achieved in this variable
int command = ' ';                                        ///< Memorizing the character to be displayed by the hand
int purpose = UNFOUND;                                    ///< Memorizing in which mode the application is used (Quiz or educationnal)
int timeOnLetter = 1;                                     ///< Memorizing the time that has to be spent on each letter
bool timerDone = false;                                   ///< Flag for the timer of the time spent on each letter


/** Setup
 */
void setup() {
  pinMode(LED_BUILTIN, OUTPUT);
  Serial.begin(BAUD);
  /** Initializing the timer to send the state to the Pi
   */
  timerSendMsg.setDelay(SEND_UPDATE_PERIODE);
  timerSendMsg.setCallback(sendTimerCallback);
  timerSendMsg.enable();
  /** Initializing the timer to handle the time spent on each letter
   */
  timerOnLetter.setDelay(TIME_ON_LETTER);
  timerOnLetter.setCallback(resetTimer);
  timerOnLetter.enable();
  /** initializing the pwm
   */
  pwm.begin();
  pwm.setPWMFreq(FREQUENCY);                              ///< Analog servos run at ~60Hz updates. 
  /** Placing every fingers to the initial position
   */
  for(int increment = 0; increment<NB_FINGERS; increment++){
    servo.servoOut('5',increment);
  }
}
/** @fn void setup()
 * @brief This function is the setup of the program.
 * @return This function doesn't return (void).
 */

void loop() {
  /** This section is executed if the arduino should send state to Pi.
   */
  if(shouldSend)
  {
    comObject.sendState(shouldRead);                      ///< Sends the state to the Pi.
  }
  /** This section is executed if the Arduino's state is not ready.
   */
  if(shouldRead == NOT_READY_TO_READ){
    /** This section is executed if the purpose is Education.
     */
    if(purpose != QUIZ){
      /** This section is executed if the hand hasn't finished it's moved
       * and the return value of servoOut() is true.
       */
      if(!moveDone && servo.servoOut(command,increment)){
        moveDone = true;                                  ///< If the code enters this section, the move is done.
      }
      /** This section is executed if the time on letter timer has elapsed.
       */
      if(timerDone){
        /** This section is executed if the move is done and
         * the return value of reverseMove() is true.
         */
        if(moveDone && servo.reverseMove(command, decrement)){
          reverseDone = true;                             ///< If the code enters this section, the reverse move is done.
          shouldRead = READY_TO_READ;                     ///< The move is finished. The arduino's state is ready.
          increment = 0;                                  ///< Increment is reset to 0.
          decrement = NB_FINGERS-1;                       ///< Decrement is reset to nb of fingers - 1.
          lastCommand = command;                          ///< Saving the actual command in memory &lastCommand.
          command = ' ';                                  ///< Command is reset to ' '.
        }
      }
      /** The the next if defines wich one of the increment or decrement to operate
       * on, depending on the conditions of the hand.
       */
      if(!moveDone){increment++;}                               ///< Incrementing
      if(timerDone && moveDone && !reverseDone){decrement--;}   ///< Decrementing
    }
    /** This section is executed if the purpose is Quiz.
     */
    else if(purpose == QUIZ){
      /** This section is executed if the last command is a character.
       */
      if(lastCommand != toAscii(' ')){
        /** This section is executed if the reverse move hasn't been done
         * and if the return value of reverseMove() is true.
         */
        if(!reverseDone && servo.reverseMove(lastCommand, decrement)){
          reverseDone = true;                             ///< If the code enters this section, the reverse move is done.
        }
        /** This section is executed if the reverse move is done
         * and if the return value of servoOut() is true.
         */
        if(reverseDone && servo.servoOut(command, increment)){
          /** This section is executed if the time on letter timer has elapsed.
           */
          if(timerDone){
            moveDone = true;                              ///< If the code enters this section, the move is done.
            shouldRead = READY_TO_READ;                   ///< The move is done. The arduino's state is ready.
            increment = 0;                                ///< Increment is reset to 0.
            decrement = NB_FINGERS-1;                     ///< Decrement is reset to nb of fingers - 1.
            lastCommand = command;                        ///< Saving the actual command in memory &lastCommand.
            command = ' ';                                ///< Command is reset to ' '.
          }
        }
      }
      /** The next if defines wich one of the increment or decrement to operate
       * on, depending on the conditions of the hand.
       */
      if(!reverseDone){decrement--;}                            ///< Incrementing
      if(timerDone && reverseDone && !moveDone){increment++;}   ///< Decrementing
    }
  }
  /** End of the not ready to read case
   */

  /** This section is executed if the arduino's state is ready to read.
   */
  if(shouldRead == READY_TO_READ){
    moveDone = false;                                           ///< Resetting moveDone to false.
    reverseDone = false;                                        ///< Resetting reverseDone to false.
    comObject.readCommand(&command, &purpose, &timeOnLetter);   ///< Reading informations about incoming command.
    /** This section is executed if the command is not empty.
     */
    if(command != toAscii(' ')){                               
      shouldRead = NOT_READY_TO_READ;                           ///< The state of the arduino is set to not ready because it received a valid command.
      timerOnLetter.setDelay(timeOnLetter*1000);                ///< Setting the delay on the time on letter timer.
      timerOnLetter.enable();                                   ///< Resetting the time on letter timer.
      timerDone = false;                                        ///< Dropping the timerDone flag.
    }
    /** The next section is executed if the state of the Arduino isn't ready to read.
     */
    else
    {
      shouldRead = READY_TO_READ;                               ///< Setting the Arduino's state to ready to read.
    }
  }
  /** The next commands updates the running timers.
   */
  timerSendMsg.update();
  timerOnLetter.update();
  delay(LOOP_DELAY);                                            ///< loop delay to cool down the processor and control the communication rate.
}
/** @fn void loop()
 * @brief This function is the main loop executed by the Arduino.
 * @return This function doesn't return (void).
 */

void sendTimerCallback(){shouldSend = true;}
/** @fn void sendTimerCallback()
 * @brief This function is executed when the communication sender timer is over.
 * @return This function doesn't return (void).
 */
void resetTimer(){timerDone = true;}                      ///< This function is executed when the time on letter timer is over.
/** @fn void resetTimer()
 * @brief This function is executed when the time on letter timer is over.
 * @return This function doesn't return (void).
 */

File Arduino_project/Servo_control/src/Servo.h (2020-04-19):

/** @file Servo.h
 * The file Servo.h contains the class Servo.
 */
#if !defined(SERVO)
#define SERVO
/** @class Servo 
 * @brief Class containing functions related to the servomotors.
 * 
 * This class contains the structures of characters and the functions used to control the servo output.
 * @author CHARBONNEAU, EMILE
 * @date 19/04/2020
 */

#include <Arduino.h>
#include <Adafruit_PWMServoDriver.h>                        ///< Library needed to control the PWM of servo drive.

// Section to change when adding servos or characters:
#define NB_LETTERS            32                            ///< Number of characters managed.
#define NB_MOTORS             10                            ///< Number of active motors.
#define NB_FINGERS            5                             ///< Number of active fingers.

// The next defined are the different articulated positions for a finger:
#define VERTICAL              0                             ///< Finger fully unfold.
#define HORIZONTAL            1                             ///< Finger with first knuckle fold.
#define A90_DEGREE            2                             ///< Finger with second knuckle fold.
#define FULLY_INCLINED        3                             ///< Finger with botch knuckles fold.

/** @brief The next defined are the different fingers implemented.
 *
 * The increment per finger is 2 because there are 2 motors per finger that requires to move.
 * This implementation eases the working principal of the function moveFinge(int,int).
 */
#define THUMB                 0
#define INDEX                 2
#define MIDDLE                4
#define RING                  6
#define LITTLE                8

/**Defining moving angles.
 */
#define NOT_INCLINED          50                            ///< Angle for a straigth knuckle.
#define INCLINED              150                           ///< Angle for an inclined knuckle.

/**The next section contains defined PWM constants.
 */
#define MIN_PULSE_WIDTH       650
#define MAX_PULSE_WIDTH       2350
#define DEFAULT_PULSE_WIDTH   1500
#define FREQUENCY             50

Adafruit_PWMServoDriver pwm = Adafruit_PWMServoDriver();    ///< Setting up the pwm object with the default address for the driver (0x40).
uint8_t servonum = 1;                                       ///< Creation of a servo driver object (PCA9685).

/** @struct character 
 * @brief Creating a structure that will hold informations relative to each character.
 */
struct character{
  int id;                                                   ///< The character in question converted in Ascii.
  int pattern[NB_FINGERS];                                  ///< The pattern in which order should the fingers move.
  int angle[NB_FINGERS];                                    ///< The angles the fingers should move to in accordance to the pattern.
} charact[NB_LETTERS];                                      ///< Creating a structure instance charact wich is an array the size of 

class Servo
{
public:
    Servo(){
        /** @brief Default constructor for the object servo.
         * 
         * This constructor initializes each character coded below in accordance to the structure character.
         * This is the structure to follow :
         * charact[int] = {{('Character id')},{pattern},{Angles}};
         */
        charact[0] = {('0'),{THUMB,INDEX,MIDDLE,RING,LITTLE},{FULLY_INCLINED,FULLY_INCLINED,FULLY_INCLINED,FULLY_INCLINED,FULLY_INCLINED}};
        charact[1] = {('1'),{THUMB,INDEX,MIDDLE,RING,LITTLE},{FULLY_INCLINED,VERTICAL,FULLY_INCLINED,FULLY_INCLINED,FULLY_INCLINED}};
        charact[2] = {('2'),{THUMB,INDEX,MIDDLE,RING,LITTLE},{FULLY_INCLINED,VERTICAL,VERTICAL,FULLY_INCLINED,FULLY_INCLINED}};
        charact[3] = {('3'),{THUMB,INDEX,MIDDLE,RING,LITTLE},{VERTICAL,VERTICAL,VERTICAL,FULLY_INCLINED,FULLY_INCLINED}};
        charact[4] = {('4'),{THUMB,INDEX,MIDDLE,RING,LITTLE},{FULLY_INCLINED,VERTICAL,VERTICAL,VERTICAL,VERTICAL}};
        charact[5] = {('5'),{THUMB,INDEX,MIDDLE,RING,LITTLE},{VERTICAL,VERTICAL,VERTICAL,VERTICAL,VERTICAL}};
        charact[6] = {('a'),{THUMB,INDEX,MIDDLE,RING,LITTLE},{VERTICAL,FULLY_INCLINED,FULLY_INCLINED,FULLY_INCLINED,FULLY_INCLINED}};
        charact[7] = {('b'),{THUMB,INDEX,MIDDLE,RING,LITTLE},{HORIZONTAL,VERTICAL,VERTICAL,VERTICAL,VERTICAL}};
        charact[8] = {('c'),{THUMB,INDEX,MIDDLE,RING,LITTLE},{A90_DEGREE,A90_DEGREE,A90_DEGREE,A90_DEGREE,A90_DEGREE}};
        charact[9] = {('d'),{INDEX,MIDDLE,RING,LITTLE,THUMB},{VERTICAL,FULLY_INCLINED,FULLY_INCLINED,FULLY_INCLINED,FULLY_INCLINED}};
        charact[10] = {('e'),{THUMB,INDEX,MIDDLE,RING,LITTLE},{FULLY_INCLINED,FULLY_INCLINED,FULLY_INCLINED,FULLY_INCLINED,FULLY_INCLINED}};
        charact[11] = {('f'),{THUMB,INDEX,MIDDLE,RING,LITTLE},{A90_DEGREE,A90_DEGREE,VERTICAL,VERTICAL,VERTICAL}};
        charact[12] = {('g'),{THUMB,INDEX,MIDDLE,RING,LITTLE},{VERTICAL,VERTICAL,FULLY_INCLINED,FULLY_INCLINED,FULLY_INCLINED}};
        charact[13] = {('h'),{THUMB,INDEX,MIDDLE,RING,LITTLE},{VERTICAL,VERTICAL,VERTICAL,FULLY_INCLINED,FULLY_INCLINED}};
        charact[14] = {('i'),{INDEX,MIDDLE,RING,LITTLE,THUMB},{FULLY_INCLINED,FULLY_INCLINED,FULLY_INCLINED,VERTICAL,FULLY_INCLINED}};
        charact[15] = {('j'),{INDEX,MIDDLE,RING,LITTLE,THUMB},{FULLY_INCLINED,FULLY_INCLINED,FULLY_INCLINED,VERTICAL,FULLY_INCLINED}};
        charact[16] = {('k'),{THUMB,INDEX,MIDDLE,RING,LITTLE},{VERTICAL,VERTICAL,VERTICAL,FULLY_INCLINED,FULLY_INCLINED}};
        charact[17] = {('l'),{THUMB,INDEX,MIDDLE,RING,LITTLE},{VERTICAL,VERTICAL,FULLY_INCLINED,FULLY_INCLINED,FULLY_INCLINED}};
        charact[18] = {('m'),{THUMB,INDEX,MIDDLE,RING,LITTLE},{FULLY_INCLINED,FULLY_INCLINED,FULLY_INCLINED,FULLY_INCLINED,FULLY_INCLINED}};
        charact[19] = {('n'),{LITTLE,RING,THUMB,INDEX,MIDDLE,},{FULLY_INCLINED,FULLY_INCLINED,FULLY_INCLINED,FULLY_INCLINED,FULLY_INCLINED}};
        charact[20] = {('o'),{THUMB,INDEX,MIDDLE,RING,LITTLE},{A90_DEGREE,A90_DEGREE,A90_DEGREE,A90_DEGREE,A90_DEGREE}};
        charact[21] = {('p'),{THUMB,INDEX,MIDDLE,RING,LITTLE},{VERTICAL,VERTICAL,VERTICAL,FULLY_INCLINED,FULLY_INCLINED}};
        charact[22] = {('q'),{THUMB,INDEX,MIDDLE,RING,LITTLE},{VERTICAL,VERTICAL,FULLY_INCLINED,FULLY_INCLINED,FULLY_INCLINED}};
        charact[23] = {('r'),{THUMB,INDEX,MIDDLE,RING,LITTLE},{FULLY_INCLINED,VERTICAL,VERTICAL,FULLY_INCLINED,FULLY_INCLINED}};
        charact[24] = {('s'),{INDEX,MIDDLE,RING,LITTLE,THUMB},{FULLY_INCLINED,FULLY_INCLINED,FULLY_INCLINED,FULLY_INCLINED,FULLY_INCLINED}};
        charact[25] = {('t'),{INDEX,MIDDLE,RING,LITTLE,THUMB},{FULLY_INCLINED,FULLY_INCLINED,FULLY_INCLINED,FULLY_INCLINED,VERTICAL}};
        charact[26] = {('u'),{THUMB,INDEX,MIDDLE,RING,LITTLE},{FULLY_INCLINED,VERTICAL,VERTICAL,FULLY_INCLINED,FULLY_INCLINED}};
        charact[27] = {('v'),{THUMB,INDEX,MIDDLE,RING,LITTLE},{FULLY_INCLINED,VERTICAL,VERTICAL,FULLY_INCLINED,FULLY_INCLINED}};
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

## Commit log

2020-02-01 First Ui elements (pause and stop button)
2020-02-05 Create Servo_control_example
    This is an example of controlling a servo sg90 with Arduino/OpenCR. In this example, the servo is controlled from 0 to 180° back and forth. This code can be easily modified to create a function that 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
2020-02-05 Added more widget to the ui and fixed layout
    [Ui_Main_Script.py]
2020-02-14 Servo control 2020/02/14
2020-02-14 Control of the servo motors 2020-02-14
2020-02-19 Added pwm servo library to project (need internet)
2020-02-19 Unit tests, new next_letter event implementation and minor bug fixes
    [Configuration.py, EventHandler.py, EventQueue.py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]
2020-02-19 New unit tests, Minor bug fixes
    [Communication.py, Event.py, EventHandler.py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]
2020-02-19 Fixed unending thread
2020-02-22 Added a comment arduino loop
2020-02-23 changed main loop on arduino and clarify code
2020-02-25 Implemented com with arduino and ui, also cleaned
2020-02-25 Fixed the directory for the image in the UI
    [Ui_Main_Script.py]
2020-02-26 intialize mechanics folder
    [Auriculaire.SLDASM, Bras de levier.SLDPRT, Index-Annulaire.SLDASM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]
2020-03-10 Fixed communication and eventhandler integration:)
    [Communication.py, EventHandler.py, Ui_Main_Script.py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]
2020-03-12 fixed some bugs in communication ending thread
    [Communication.py, EventHandler.py, Ui_Main_Script.py]
2020-04-07 Fixed Tk() command not running on linux and path
    [Ui_Main_Script.py]
2020-04-07 Fixed for real Tk() command
    [Ui_Main_Script.py]
2020-04-08 Fixed communication on linux platform
    [Communication.py]
2020-04-08 Update README.md
    Add how to prepare a Raspberry Pi 3b+ to run the program
2020-04-13 Fixed quiz details related to UI
    [EventHandler.py, Quiz.py, TextAnalyser.py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]
2020-04-16 Fixed one bug according to disabling radiobutton
    [EventHandler.py, Ui_Main_Script.py]
2020-04-17 Added the reverseMove functioAdded the reverseMove functionn
    [Servo.h, main.ino]
2020-04-17 Fixed return value ìn arduino Communication func
    [CommunicationArduino.h]
2020-04-17 Fixed minor bug from UI
    [Ui_Main_Script.py]
2020-04-18 Added the electrical schema
    Schema visualising the connections between the Arduino Mega 2560, Servo Driver PCA9685 and the servo motors.
2020-04-18 Updated the elctrical schematics
2020-04-18 Corrected an event handler bug
    [EventHandler.py]
2020-04-19 Commented the servo.h and main.ino files
2020-04-19 Commented the Arduino code and generated Doc. html
2020-04-20 Fixed mechanics paths
    [90001A403_TYPE 18-8 STAINLESS STEEL HEX NUT.SLDPRT, 90044A242_BLACK-OXIDE ALLOY STEEL SOCKET HEAD SCREW.SLDPRT, 90087A103_THRD-CUTTING SCREW FOR METAL PLASTIC 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]
2020-04-20 Finishing mec folder
    [BOM.xlsx]
2020-04-20 Fixed a comment in CommunicationArduino.h
    [CommunicationArduino.h]
